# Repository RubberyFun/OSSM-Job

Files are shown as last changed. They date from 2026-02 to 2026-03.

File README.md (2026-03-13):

# OSSM Job 
#### This is a drop-in attachment to quickly and reversibly convert your OSSM to a piston driven pneumatic stroker device
<p align="center">
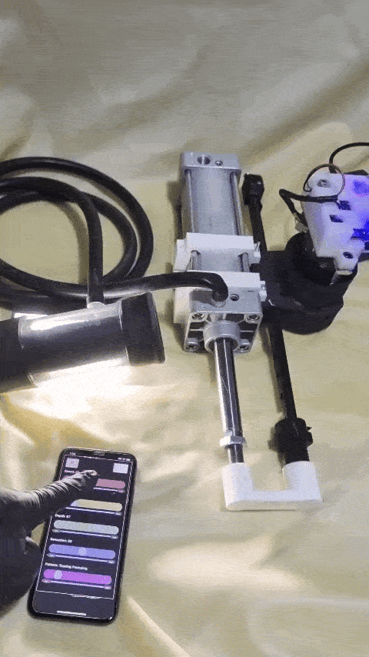
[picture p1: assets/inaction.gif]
V1 in action
    
</p>

## Overview
The piston attaches to the OSSM faceplate with [3d printed clamps](STL/OSSM-Job-Piston-Clamps.stl) and screws. A 3d printed [linkage](STL/OSSM-Job-Arm-Linkage.stl) attaches the piston arm to the OSSM arm...now the piston goes back and forth.  The 3d printed [air adaptor](STL/OSSM-Job-Piston-Hose-Adaptor.stl) screws into the piston and the hose is stuck on top of it.  

The other end of the hose attaches to [the receiver](STL/OSSM-Job-Receiver-M.stl).  You could use a receiver from any name brand stroker...otherwise, files are included to [make your own](STL/OSSM-Job-Receiver-M.stl)!  A sheath is stretched inside the receiver and folded over the outside of each end to keep in place.  The cap is put on the far end and a one-way valve attached to [the cap](STL/OSSM-Job-Receiver-cap.stl).  Add some carrots and you've got a stew baby!
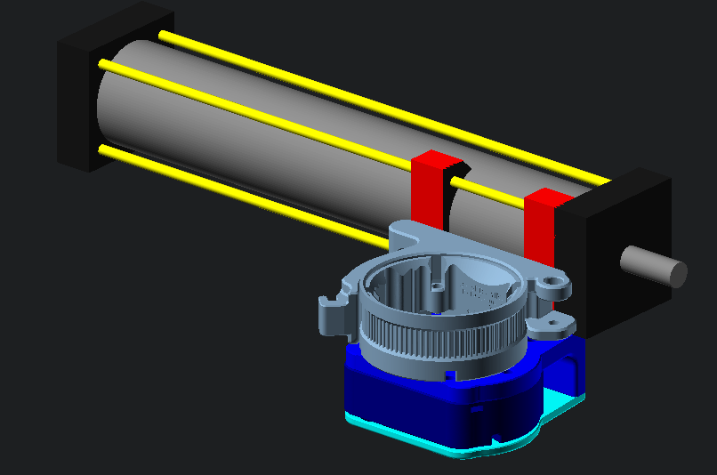
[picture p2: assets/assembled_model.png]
assembly


## 3d printed parts:
- [top](STL/OSSM-Job-Piston-Clamps-SC50.stl) and bottom clamps for securing the piston (4 pieces total)
- [linkage](STL/OSSM-Job-Arm-Linkage-SC50.stl) for the toy end of the arm.
- [air adaptor](STL/OSSM-Job-Piston-Hose-Adaptor-SC50.stl) for connecting piston to hose
- [pitclamp mini](https://github.com/KinkyMakers/OSSM-hardware/blob/main/Documentation/ossm/Hardware/standard-printed-parts/pitclamp) for quick transfer of the OSSM motor
#### optional:
- [receiver](STL/OSSM-Job-Receiver-M.stl) and [cap](STL/OSSM-Job-Receiver-cap.stl)
- alternative [autoblow type receiver with a wider bottom](STL/OSSM-Job-Receiver-M-flared.stl) and [cap](STL/OSSM-Job-Receiver-cap-flared.stl)

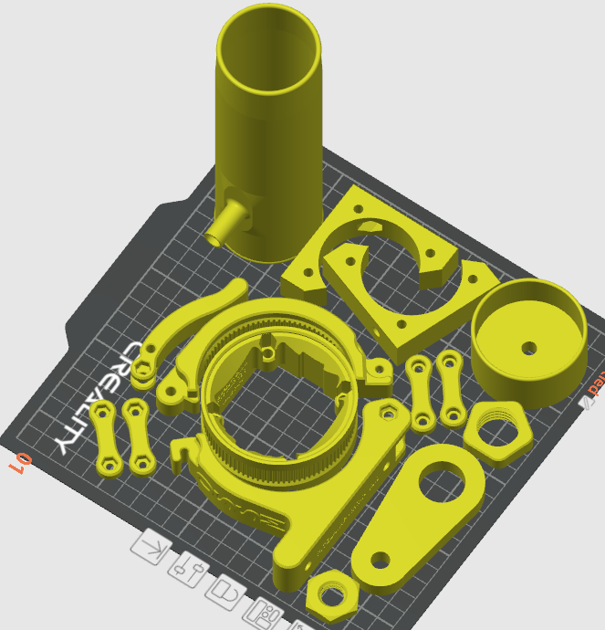
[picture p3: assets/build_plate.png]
build plate


## BOM
In addition to the printed parts above you will need to buy some parts for this to work, most importantly a piston:

- [SC50-200 Piston like this one from amazon for $35](https://www.amazon.com/HNJPC-Cylinder-Pneumatic-Industrial-Automation/dp/B0BZCL5859)
- Nuts & Bolts: ([for the pitclamp](https://github.com/KinkyMakers/OSSM-hardware/blob/main/Documentation/ossm/Hardware/standard-printed-parts/pitclamp))
    - 2 M6x15 screws to join the clamps to the mount (M5 would work)
    - 2 M6 nuts for the above screws (M5 would work)
    - 1 M5x20 Socket Cap Head Bolt for hinge
    - 1 M5 Hex Nut for hinge
    - 2 M4x25 Socket Cap Head Bolts for latch
    - 1 M4x12 or M4x10 Socket Cap Head Bolt for handle
    - 3 M4 Hex Nuts for latch and handle
&nbsp;
- Optional: a pre-built receiver setup like 
    - [The original Venus 200 receiver for $39](https://venusformen.com/shop/receiver/)
    - [The Autoblow Vacuglide for $69](https://autoblow.com/product/vacuglide-large-accessories-pack/)
    - [A SeriousKit receiver could be converted for £150](https://www.seriouskit.com/collections/spts/products/see-through-lined-spt)
#### ...or use the included 3d printed receiver with:
- Receiver sleeves (also a few options here):
    - [Original venus sleeves for about \$5 each](https://venusformen.com/shop/liner-material/)
    - [Autoblow sleeves for \$20](https://autoblow.com/product/vacuglide-power-pulse-sleeve/ )
    - [Serious Kit transparent liners for £12.75: ](https://www.seriouskit.com/products/see-through-liners?variant=47351005774123 )
    - [Buy a bit of latex \$12](https://mjtrends.com) and make your own! \$12 is enough for 24 sheaths but requires latex crafting skills.
    - [A latex 34-42 bicycle tube for \$19](https://us.challengetires.com/products/latex-inner-tube) Only the bigger sizes will work.  The jury is out whether this is worth it...standard butyl tires are cheap but thick, TPU isn't stretchy enough, and latex tubes are rare in big enough sizes.  Anybody know where to buy thin latex tubing at 1.5" / 40mm diameter?
- Check valves from \$5 - \$15 (there are a few options though you might need to adjust the diameter of the stem to fit some kinds):
    - [Original autoblow duckbill valve the receiver design is based on](https://autoblow.com/product/vacuglide-nipples-2-set/ )
    - [cheapo amazon duckbill valve](https://www.amazon.com/Compatible-Replacement-Accessories-Signature-Smartpump/dp/B0CP16F4VF)
    - [push-to-fit check valve](https://www.amazon.com/Bwintech-Straight-Pneumatic-Connect-Compressor/dp/B0CFTZZ8B2  )
- a flexible hose with in inner diameter of 10mm (or 3/8" in freedom units).  
    - [silicone tube from amazon for \$14](https://www.amazon.com/dp/B0CYSX8HB9) or [latex hose from amazon for $8](https://www.amazon.com/Feelers-Natural-Speargun-Slingshot-Catapult/dp/B093WBLZMP)

## Demonstration video

<video controls width="100%"> <!-- Sadly this html only works on github pages, not github.com proper -->
  <source src="https://rubberyfun.github.io/OSSM-Job/assets/inaction.mp4" type="video/mp4" controls>
  Your browser does not support the video tag.
</video> 

[Link to the demonstration video](https://rubberyfun.github.io/OSSM-Job/assets/inaction.mp4)

## The devil is in here:
- You will probably want to add another [Pitclamp Mini](https://github.com/KinkyMakers/OSSM-hardware/tree/main/Documentation/ossm/Hardware/standard-printed-parts/pitclamp) to your OSSM so it can be quickly converted from its regular setup to a stroker.  It's a common upgrade, endorsed by Research + Desire.
- You're going to want to keep the depth centered in the OSSM range so it doesn't bottom out.  There is a "stroker mode" setting in [OSSM-Possum](https://github.com/RubberyFun/OSSM-Possum) that will do this for you automatically.
- You may hear a clicking sound from your OSSM motor.  This is likely the belt slipping.  The piston has the potential to need higher torque than the OSSM is designed for and you may need to tighten your belt.
- If the piston arm is moved to either extreme before the OSSM is turned on it may be under extra tension and convince the OSSM it's stuck.  It's best to start the arm in the middle of the stroke when powering on the OSSM.
- It doesn't matter which end of the piston you screw the hose adaptor to.  It operates much quieter if you remove any other adapter from the other port so it has as much airflow as possible.
- You will probably want to add a check valve / one-way valve to the pressure tube to allow air to escape.  A dedicated device to keep receiver pressure consistent is in the works.
- If you prefer a wider entrance like the Autoblow or will be using those liners: use the STLs ending in "-flared".  Or to make your own STL: set ```receiver_base_flare``` at the top of [scad/receiver.scad](scad/receiver.scad) to 10 (which signifies a 10mm wider diameter at the base)
- you will need supports for the hose valve stem. Automatic might work for you if you keep them from roughing up the front of the receiver, otherwise try painting them on
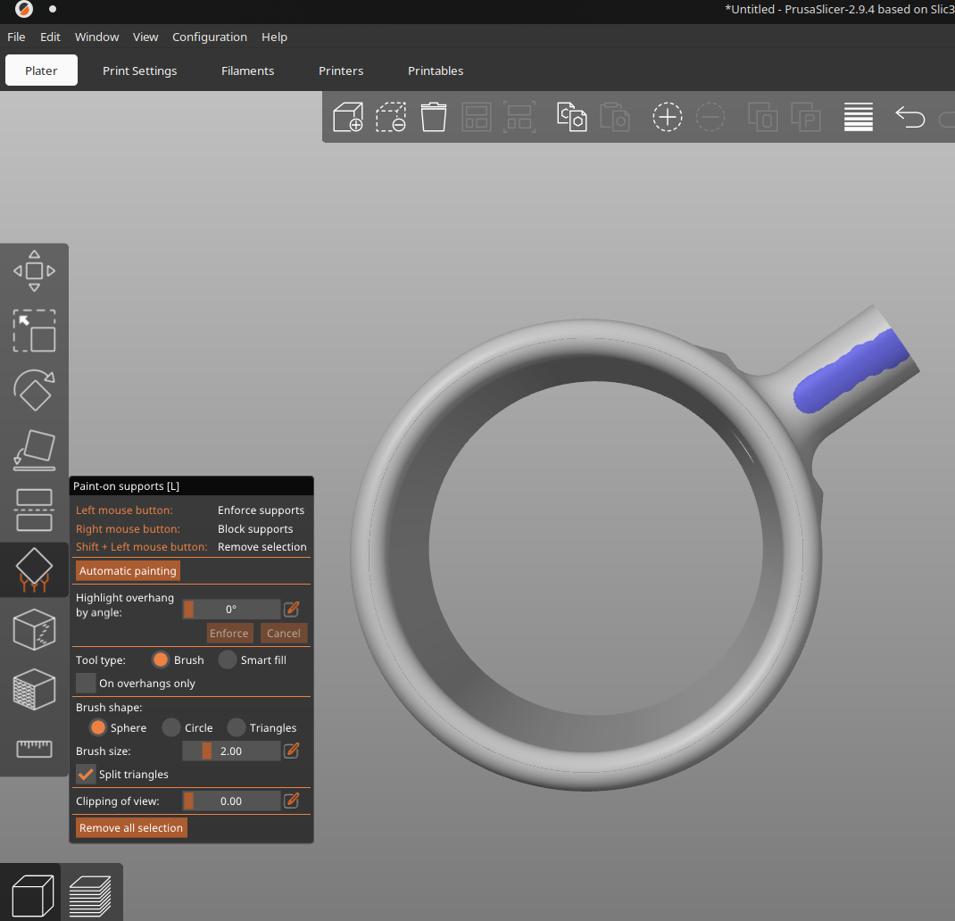
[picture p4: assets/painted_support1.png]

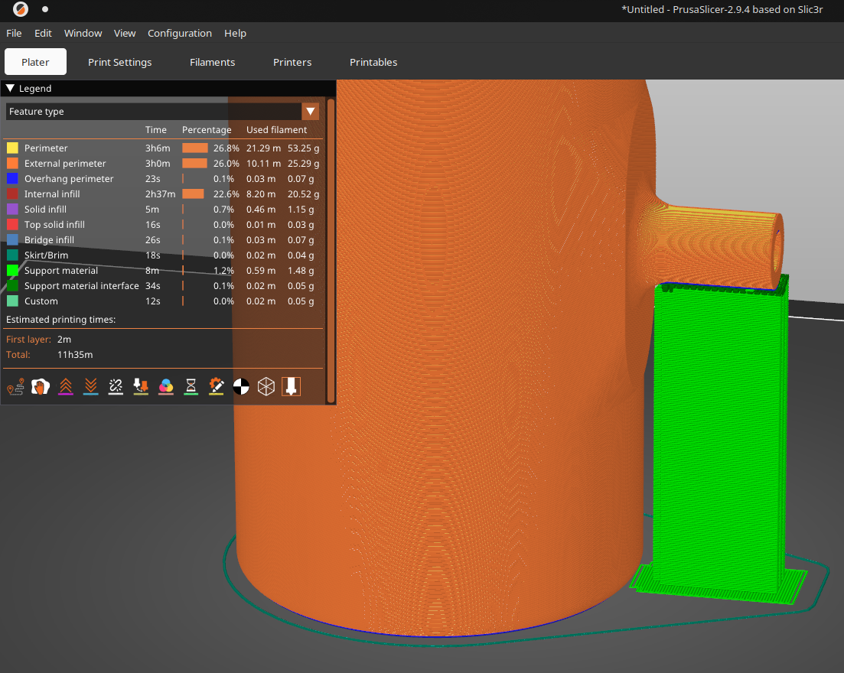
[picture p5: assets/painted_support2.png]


## Customization
- This is designed to be open source and not need a commercial CAD program.  It uses OpenSCAD which uses code for cad.  This workflow is not for everybody, but it does maximize shareability and file simplicity. (But fillets are a bitch).
- To make customizations you will need to [download OpenSCAD](https://openscad.org) and also [install the BOSL2 library](https://github.com/BelfrySCAD/BOSL2?tab=readme-ov-file#installation)
- You may find a dedicated code editor like [VS Code](https://code.visualstudio.com/) more convenient for scad files

## Related
- For a dedicated piston driven stroker [check out Diglet48's project](https://github.com/diglet48/toy-designs/tree/main/SC63%20pneumatic%20stroker) that inspired this one.  It's a much sturdier belt design.
- Credit goes to Frayd for the V2 concept using a Pitclamp and the support bars of the cylinder.  It is a much more efficient setup than V1.
- Want to control it wirelessly?  Check out the companion app featured in the above video [OSSM-Possum.
OSSM Possum](https://github.com/RubberyFun/OSSM-Possum)
- Want to use it hands free?  [Check out the OSSMount!
OSSMount](https://github.com/RubberyFun/OSSMount)
- Obviously you should know about the engine that drives this contraption [the OSSM](https://github.com/KinkyMakers/OSSM-hardware)

## Fine print

I made this for people to enjoy...no strings attached, no cost, no in-app advertising.  [The code is open-source, posted on Github](https://github.com/RubberyFun/OSSM-Job).

[OSSM Job](https://github.com/RubberyFun/OSSM-Job) © 2026 by [Claus Macher](https://rubberyfun.com) is licensed under [CC BY-SA 4.0](https://creativecommons.org/licenses/by-sa/4.0/).  It basically means you can do whatever you want with the code but anything you make with it should include an attribution and keep the same license.  Yes, that means you can make money off your remix but don't just copy the code and call it a day.

This is not directly affiliated with Kinky Makers or their products in any way...I just think they're OSSM.

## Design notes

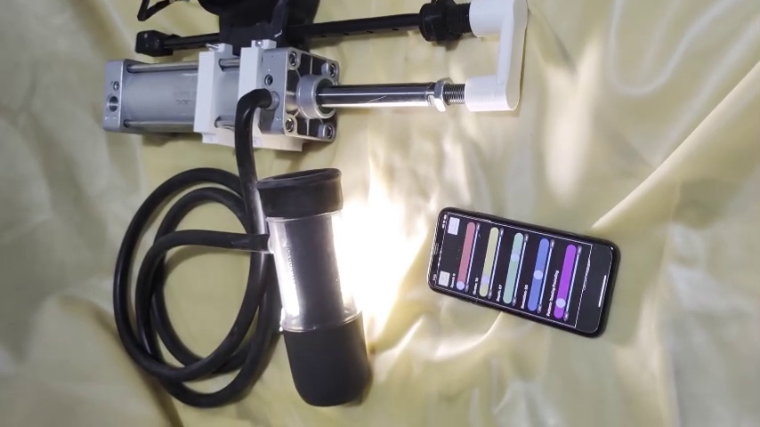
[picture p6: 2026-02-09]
assets/hardware1.png

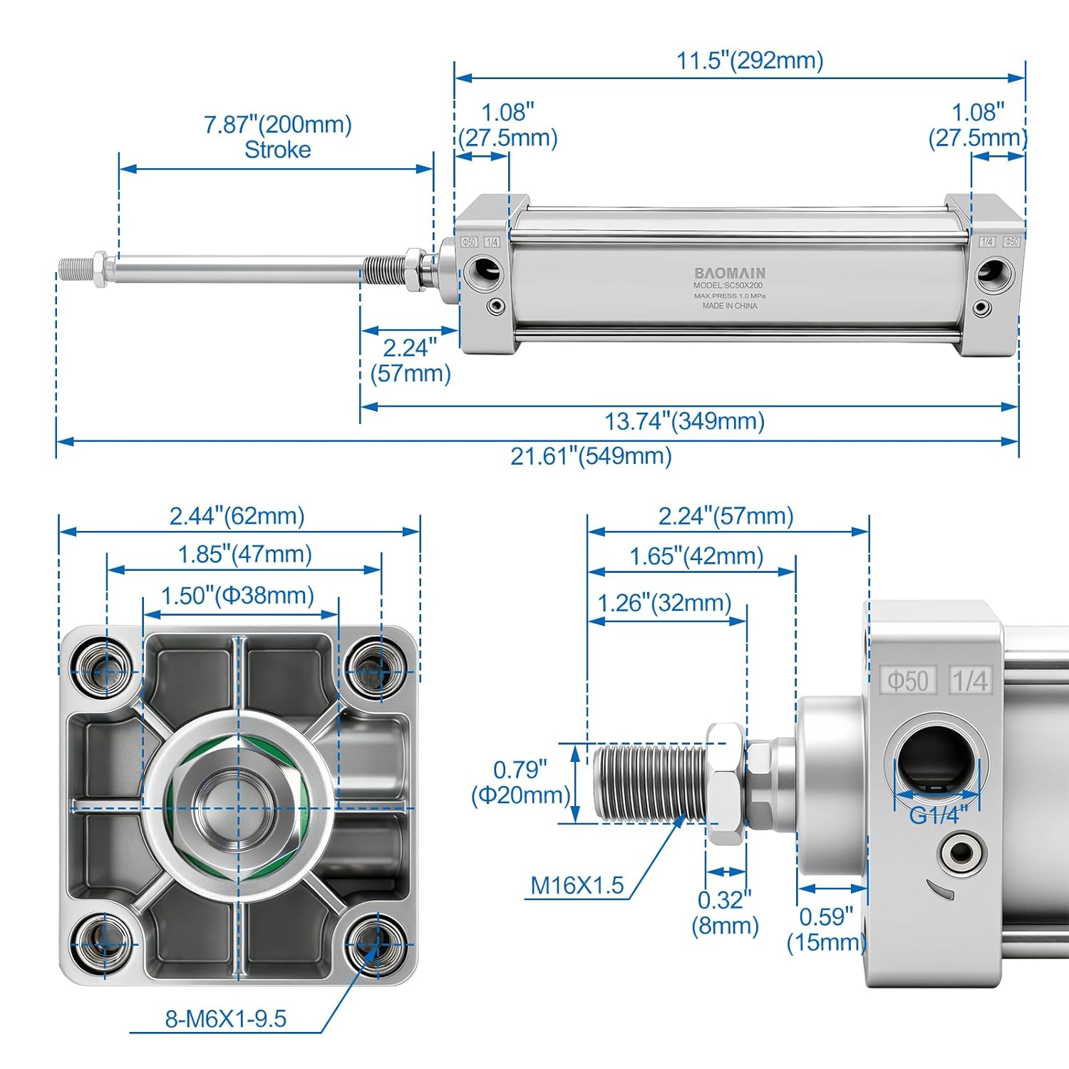
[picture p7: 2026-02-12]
assets/50x200 piston dimensions.jpg

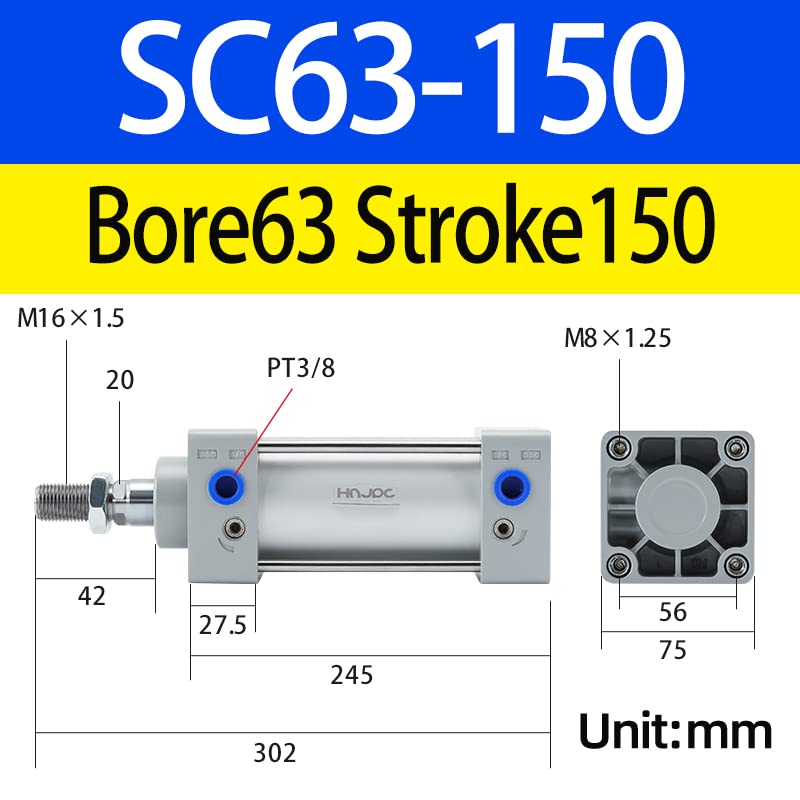
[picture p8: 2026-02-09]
assets/63x150 piston dimensions.jpg

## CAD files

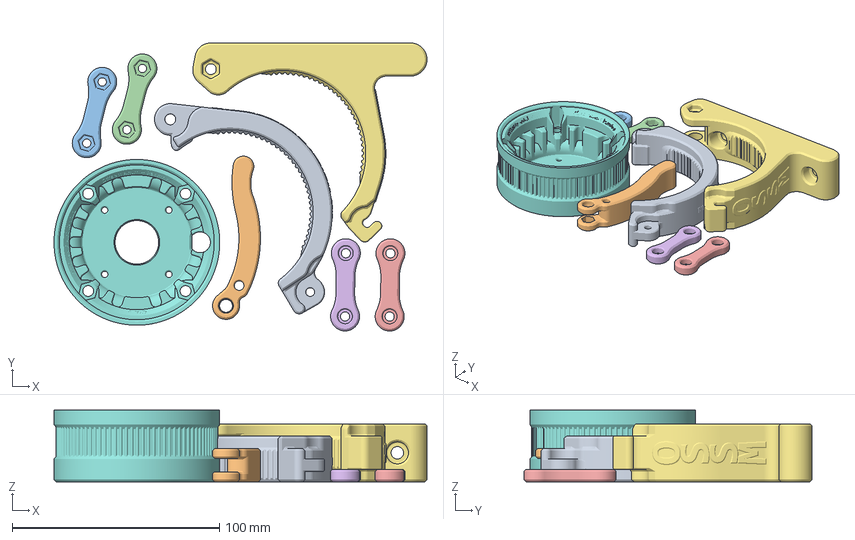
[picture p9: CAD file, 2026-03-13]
3mf for PrusaSlicer/OSSM - Base - PitClamp Mini.3mf
180.1 x 139.1 x 34.5 mm
OSSM - Base - PitClamp Mini - Upper V1.1.stl
OSSM - Base - PitClamp Mini - Handle.stl
OSSM - Base - PitClamp Mini - Dogbone Nuts.stl x 2
OSSM - Base - PitClamp Mini - Dogbone Bolts.stl x 2
OSSM - Base - PitClamp Mini - Lower V1.1.stl
OSSM - Mounting Ring - PitClamp Mini - 42AIM V1.1.stl

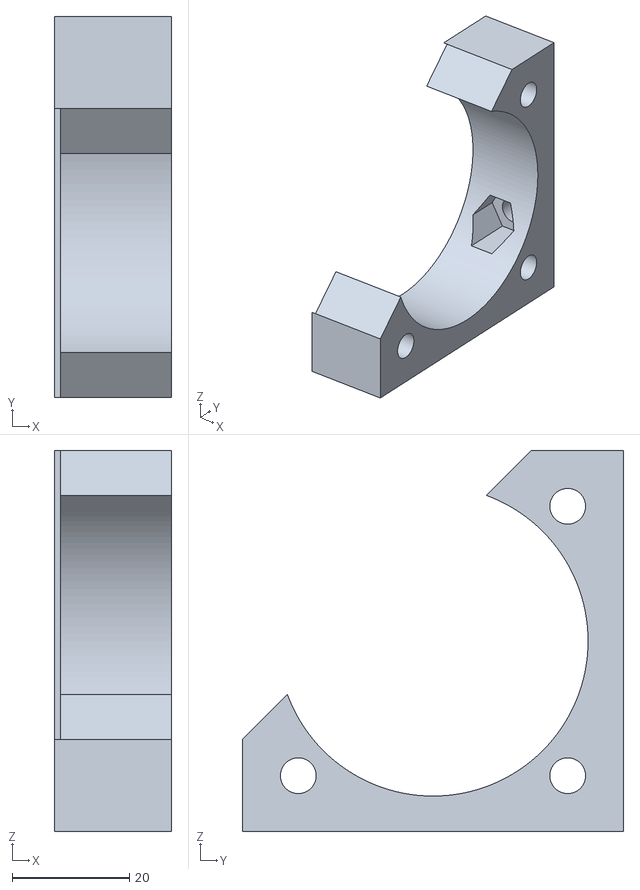
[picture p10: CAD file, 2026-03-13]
STL/OSSM-Job-Piston-Clamps-SC50.stl
20.0 x 65.1 x 65.1

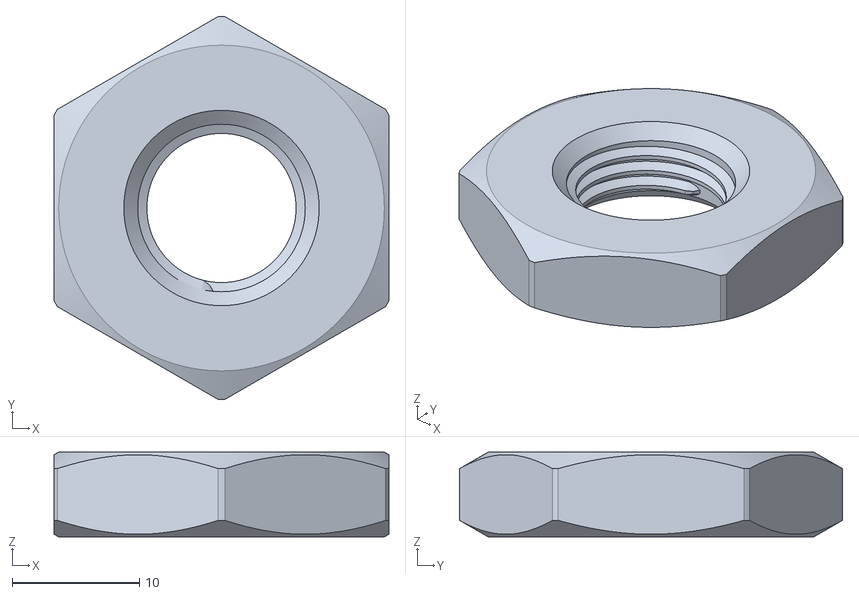
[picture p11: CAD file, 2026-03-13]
STL/piston nuts/G1_4.stl
26.3 x 30.1 x 6.67

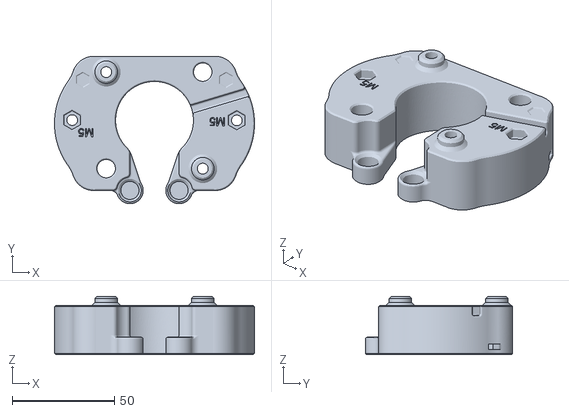
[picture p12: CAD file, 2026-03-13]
STL/reference/OSSM - Actuator - Body - Middle.stl
97.7 x 72.0 x 28.4

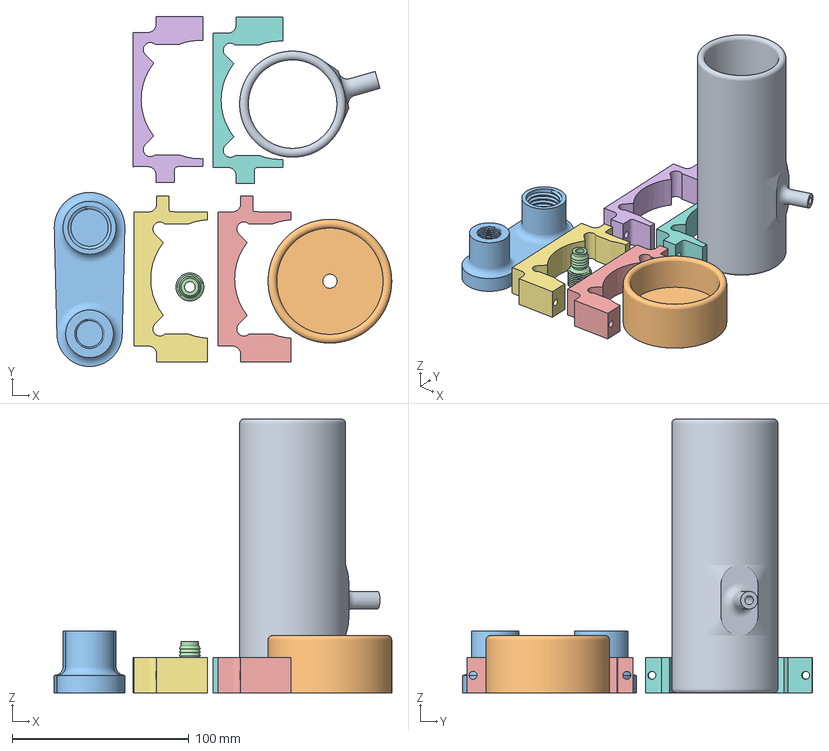
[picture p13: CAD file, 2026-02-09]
v1/3mf/OSSM-Job-SC63-w-receiver.3mf
191.0 x 198.0 x 155.0 mm
OSSM-Receiver.stl
OSSM-Receiver-cap.stl
arm-link2.stl
air-interface.stl
ossm-piston-clamp2.stl x 2
ossm-piston-clamp1.stl x 2

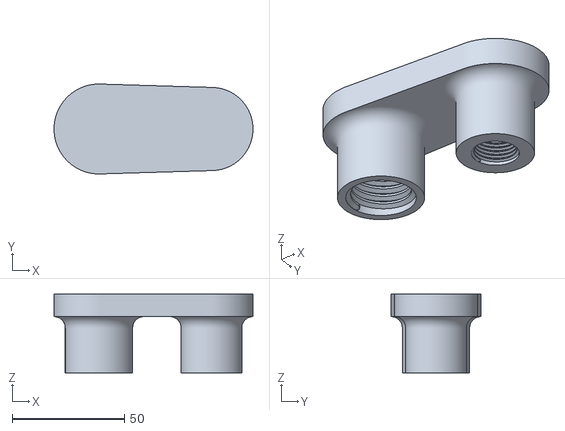
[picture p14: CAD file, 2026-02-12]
v1/stl/OSSM-Job-Arm-Linkage-SC50.stl
88.5 x 40.0 x 35.0

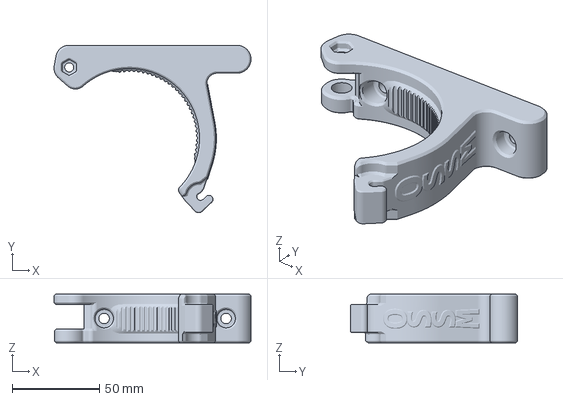
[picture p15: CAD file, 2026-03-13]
3mf for PrusaSlicer/OSSM - Base - PitClamp Mini - Lower V1.1.3mf
113.1 x 96.1 x 28.0 mm

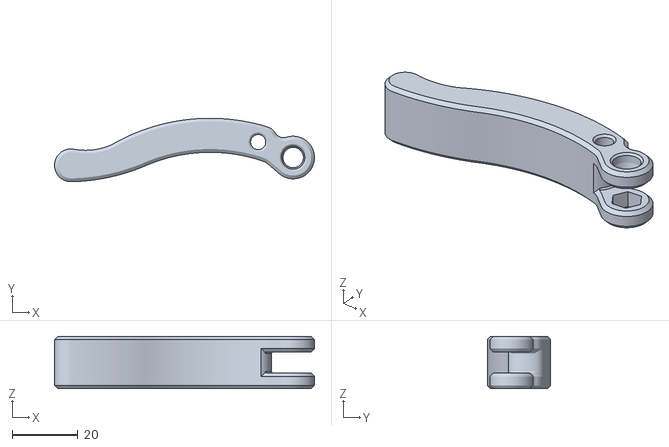
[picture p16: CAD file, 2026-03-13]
STL/pitclamp mini/OSSM - Base - PitClamp Mini - Handle.stl
79.3 x 19.3 x 16.0

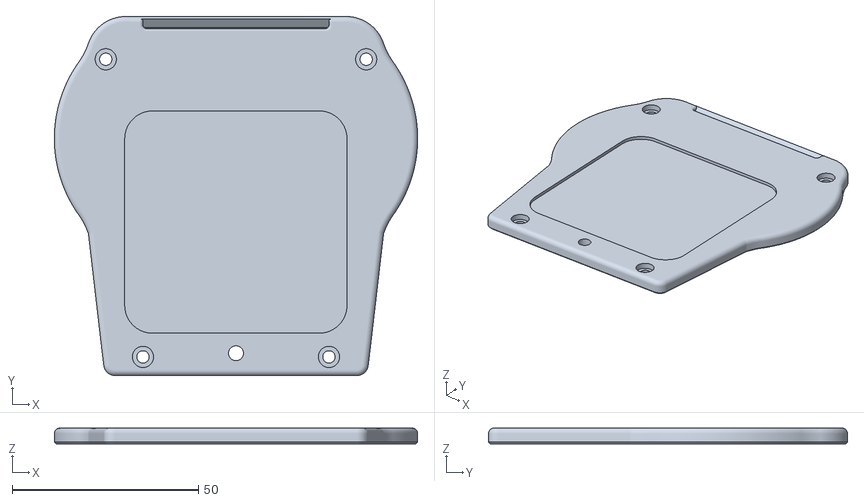
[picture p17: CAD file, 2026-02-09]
STL/reference/ossm_cover_blank.stl
97.7 x 96.5 x 4.30

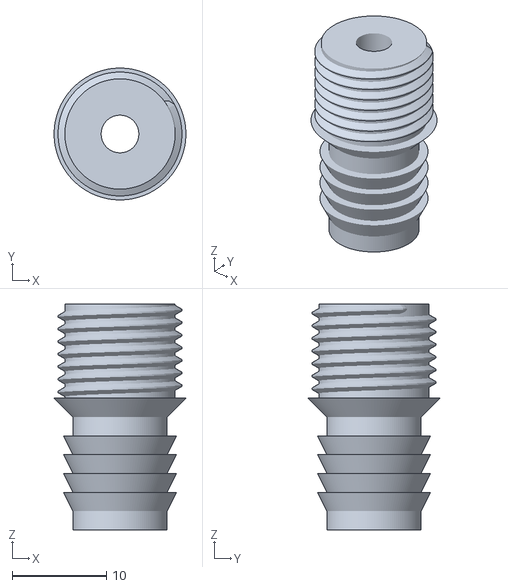
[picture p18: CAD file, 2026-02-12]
v1/stl/OSSM-Job-Piston-Hose-Adaptor-SC50.stl
14.0 x 14.0 x 24.0

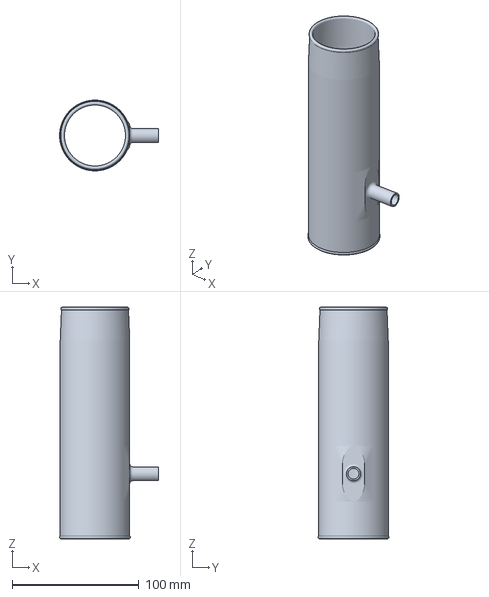
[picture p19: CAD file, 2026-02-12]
3mf for PrusaSlicer/OSSM-Job-Receiver-M-thin wall.3mf
77.9 x 55.8 x 182.9 mm

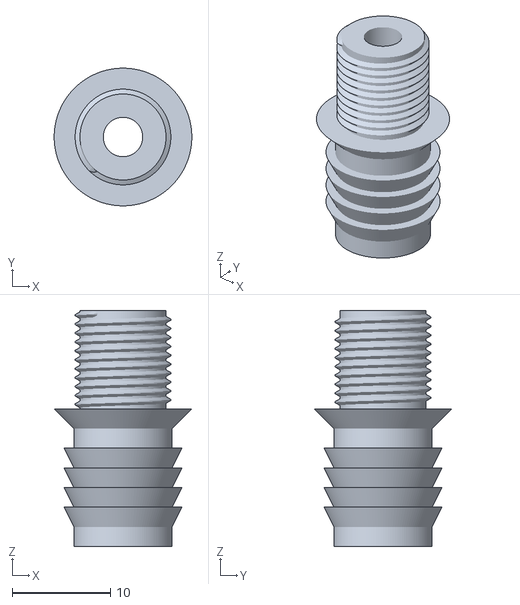
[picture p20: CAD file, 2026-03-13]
STL/OSSM-Job-Piston-Hose-Adaptor SC32.stl
14.0 x 14.0 x 24.0

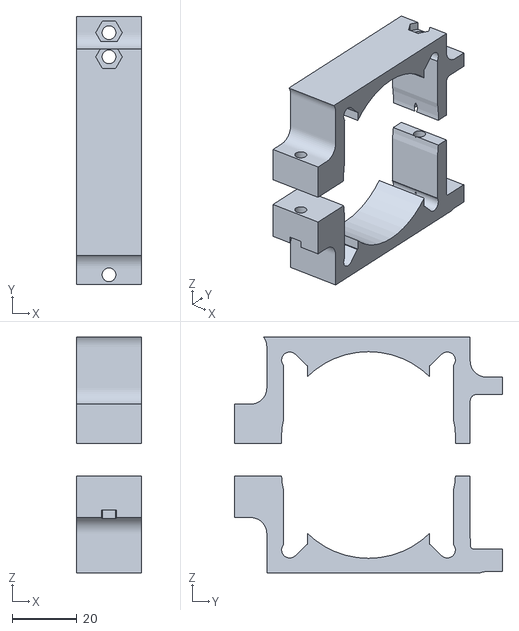
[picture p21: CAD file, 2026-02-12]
v1/stl/OSSM-Job-Piston-Clamps-SC50.stl
20.0 x 83.0 x 73.0

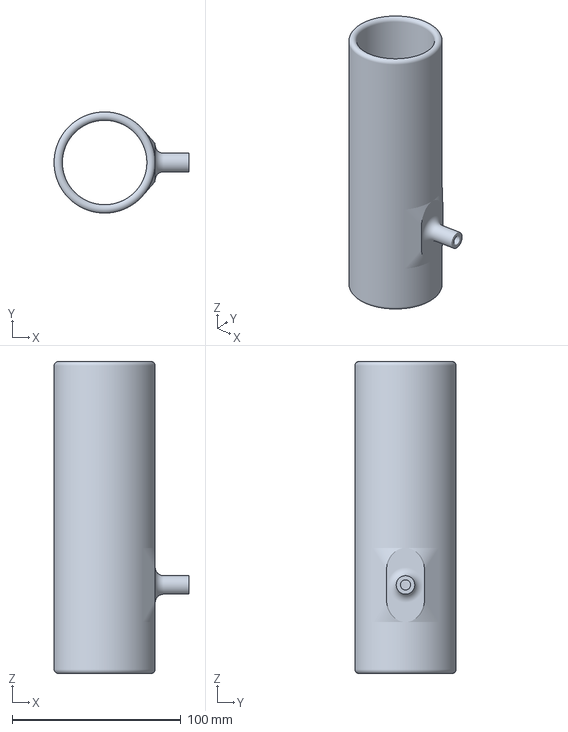
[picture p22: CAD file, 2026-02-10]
3mf for PrusaSlicer/OSSM-Job-Receiver-M.3mf
80.0 x 60.0 x 185.0 mm

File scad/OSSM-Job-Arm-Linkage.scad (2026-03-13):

include <BOSL2/std.scad>
include <BOSL2/screws.scad> 
$fn=128;
top_d = 24;  
top_pitch = 3; //M24x3 OSSM thread
bottom_d = 16;
bottom_pitch=1.5;  //sc32 = M10x1.25, sc50 = M16x1.5
wall = 1;
ossm_height = 25;
arm_height = 10;
arm_space = 60; //55 for sc32, 60 for SC50, 65 for SC63
fillet = 20;

//arm
difference() {
union() {
cylinder(h=arm_height,d=top_d+fillet);   
translate([arm_space/2,0,arm_height/2]) {
    points = [
        [-arm_space/2,top_d/2 + fillet/2],
        [arm_space/2,top_d/2 - (top_d - bottom_d)/2 + fillet/2],
        [arm_space/2,-top_d/2 + (top_d - bottom_d)/2 - fillet/2],
        [-arm_space/2,-top_d/2 - fillet/2],
    ];
    linear_extrude(height=arm_height,center=true)
    polygon(points);
}
translate([arm_space,0,0])
cylinder(h=arm_height,d=bottom_d+fillet);    
}
cylinder(h=arm_height*2+1,d=top_d,center=true);   

translate([arm_space,0,0])
cylinder(h=arm_height*2+1,d=bottom_d,center=true);    
}

//ossm nut
 translate([arm_space * -1,0,0]) {
  nut(str("M",top_d,"x",top_pitch),thickness=arm_height*1.5);
 }
 
 
//cylinder nut
 translate([arm_space * 2,0,0])

nut(str("M",bottom_d,"x",bottom_pitch),thickness=arm_height);

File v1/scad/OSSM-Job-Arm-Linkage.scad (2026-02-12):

include <BOSL2/std.scad>
include <BOSL2/screws.scad> 
$fn=128;
top_d = 30;
bottom_d = 27;
hull_cutoff = 10;
wall = 1;
ossm_height = 25;
arm_height = 10;
arm_space = 50; //60 for SC63
fillet = 20;

module round_fillet(d, size, half=false) {
    difference() {
        cylinder(d2=d + size/2, d1=d, h=size/4);
        torus(od=d + size, id=d);
        if (half) {
            translate([-(d+size/2)/2,0,0]) cube([d+size/2,d+size/2,size/2], center=true);
        }
    }
}


difference() {
    union() {
        cylinder(h=ossm_height+arm_height,d=top_d);    
            translate([0,0,ossm_height - fillet/4]) 
                round_fillet(d=top_d, size=fillet, half=false);
        
                translate([0,0,ossm_height])  cylinder(h=arm_height,d=top_d+ fillet/2);    

    }
    translate([0,0,ossm_height]) screw_hole("M24x3", length=ossm_height,anchor=TOP,thread=true, bevel1=0, $slop=0);
}

//arm
translate([arm_space/2,0,ossm_height + arm_height/2]) {
    points = [
        [-arm_space/2,top_d/2 + fillet/4],
        [arm_space/2,top_d/2 - (top_d - bottom_d)/2 + fillet/4],
        [arm_space/2,-top_d/2 + (top_d - bottom_d)/2 - fillet/4],
        [-arm_space/2,-top_d/2 - fillet/4],
    ];
    linear_extrude(height=arm_height,center=true)
    polygon(points);
}

translate([arm_space,0,0])
difference() {
    union() {
        cylinder(h=ossm_height+arm_height,d=bottom_d);    
        //scale([1,bottom_d/(bottom_d + fillet/4),1])
            translate([0,0,ossm_height - fillet/4]) 
                rotate([0,0,180])
                    round_fillet(d=bottom_d, size=fillet, half=false);
        
        translate([0,0,ossm_height]) cylinder(h=arm_height,d=bottom_d+fillet/2);    

    }
    translate([0,0,ossm_height]) screw_hole("M16x1.5", length=ossm_height,anchor=TOP,thread=true, bevel1=0, $slop=0.1);
}

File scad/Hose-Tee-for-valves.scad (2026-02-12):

include <BOSL2/std.scad>
include <BOSL2/screws.scad> 
$fn=128;



translate([-5,0,0])
difference() {
    union() {
        cylinder(d=14,h=5);

        rotate([0,0,180]) barb(ezprint=true);
        //translate([2.5,2.5,2.5]) rotate([90,180,0]) barb(hose_id=5, wall_thickness=1, barbs=4, ezprint=true);
        translate([0,4.5,2.5]) rotate([90,180,0]) barb(ezprint=true, bevel=false);
        translate([0,0,5]) rotate([0,180,0]) barb(ezprint=true);
    }

    translate([0,0,-.5])cylinder(d=6,h=6);
    translate([0,0,2.5]) rotate([-90,0,0]) cylinder(d=6,h=17);
    translate([7.5,0,0]) cube([5,15,32],center=true);
}



module barb(hose_od = 14, hose_id = 10, swell = 2, wall_thickness = 2, barbs = 4, barb_length = 2, shell = true, bore = true, bevel=true, ezprint = false) {
    id = hose_id - (2 * wall_thickness);
    translate([0, 0, -((barb_length * (barbs + 3)))])
    difference() {
        union() {
            if (shell == true) {
                cylinder(d = hose_id, h = barb_length);
                for (z = [1 : 1 : barbs]) {
                    translate([0, 0, z * barb_length]) cylinder(d1 = hose_id, d2 = hose_id + swell, h = barb_length);
                }
                translate([0, 0, barb_length * (barbs + 1)]) cylinder(d = hose_id, h = barb_length*barbs/2 );
                    //bevel for strength - implemented as another barb
                    if (bevel) translate([0, 0, barb_length * (barbs + 2)]) cylinder(d1 = hose_id, d2 = hose_id + swell*2, h = barb_length);
            }
        }
        if (bore == true) {
            translate([0, 0, -1]) cylinder(d = id, h = (barb_length * (barbs + 1)) +  barb_length*(barbs + 4));
        }
        if (ezprint == true) {
            difference() {
                cylinder(d = hose_id + (swell * 3), h = (barb_length * (barbs + 1)));
                translate([swell, 0, 0]) cylinder(d = hose_id + (swell * 2), h = (barb_length * (barbs + 1)));
            }
        }
    }
}

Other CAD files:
STL/pitclamp mini/OSSM - Base - PitClamp Mini - Lower V1.1.stl
STL/OSSM-Job-Arm-Linkage-SC32.stl
STL/pitclamp mini/OSSM - Base - PitClamp Mini - Dogbone Nuts.stl
v1/stl/OSSM-Job-Piston-Hose-Adaptor-SC63.stl
scad/OSSM-Job-Piston-Clamps.scad
3mf for PrusaSlicer/OSSM-Receiver-and-cap-flared.3mf
3mf for PrusaSlicer/OSSM-Receiver-and-cap.3mf
STL/Hose-Tee-for-valves-1-4.stl
STL/Hose-Tee-for-valves-3-8.stl
STL/OSSM - 24mm Nut - 5 Sided.stl
STL/OSSM-Job-Arm-Linkage-SC50.stl
STL/OSSM-Job-Piston-Clamp-SC32.stl
STL/OSSM-Job-Piston-Hose-Adaptor-SC50.stl
STL/pitclamp mini/OSSM - Base - PitClamp Mini - Dogbone Bolts.stl
STL/pitclamp mini/OSSM - Base - PitClamp Mini - Upper V1.1.stl
STL/pitclamp mini/OSSM - Mounting Ring - PitClamp Mini - 57AIM V1.1.stl
STL/pitclamp mini/OSSM - Mounting Ring - PitClamp Mini - iHSV57.stl
scad/OSSM-Job-Piston-Hose-Adaptor.scad
scad/OSSM-Job-Receiver-and-Cap.scad
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

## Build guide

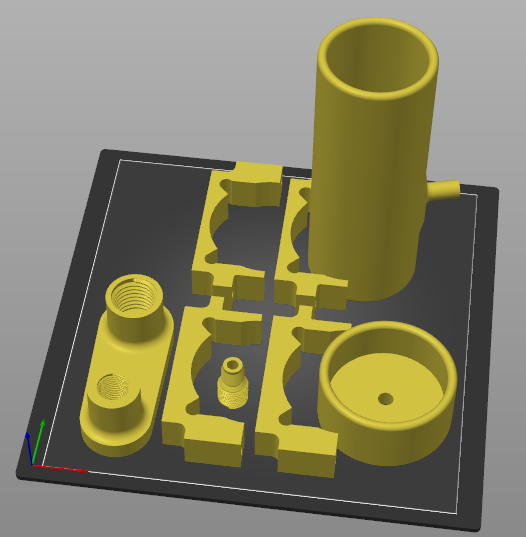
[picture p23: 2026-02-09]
v1/build_plate.png

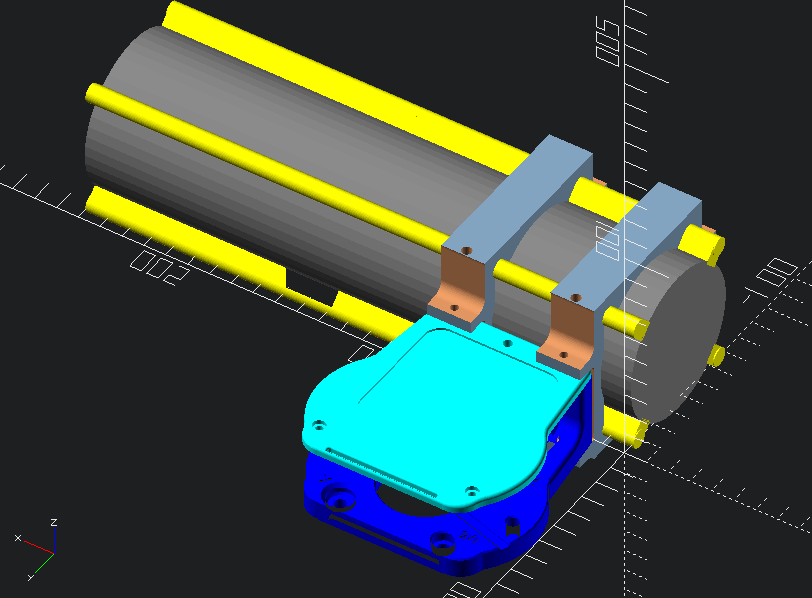
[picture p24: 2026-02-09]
v1/assembled_model.png

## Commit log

2026-02-09 OSSM Job, Claus
    [OSSM-Job.3mf, OSSM-Receiver-and-cap-flared.3mf, OSSM-Receiver-and-cap.3mf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]
2026-02-09 autoblow receiver stl
2026-02-09 screw this
2026-02-10 updates from testing, consistant file names
    [OSSM-Job-Arm-Linkage.scad, OSSM-Job-Arm-Linkage.stl, OSSM-Job-Piston-Clamps.scad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]
2026-02-10 S M L. You want fries with that?
    [OSSM-Job-Receiver-M.3mf, OSSM-Job-Receiver-and-Cap.scad]
2026-02-11 back to m4. cheating with nuts
    [OSSM-Job-Piston-Clamps.scad, OSSM-Job-Piston-Clamps.stl]
2026-02-12 re-tooled for SC50-200 piston
    [Hose-Tee-for-valves-1-4.stl, Hose-Tee-for-valves-3-8.stl, Hose-Tee-for-valves.scad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]
2026-03-13 V2 based on Frayds mounting
    [G1_4.stl, OSSM - 24mm Nut - 5 Sided.stl, OSSM - Actuator - Body - Middle.stl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]
2026-03-13 6mm arms
    [OSSM-Job-Piston-Clamps-SC50.stl, OSSM-Job-Piston-Clamps.scad]
2026-03-13 sleeve updates
    [OSSM-Job-Piston-Clamps-SC50.stl, OSSM-Job-Piston-Clamps.scad]
